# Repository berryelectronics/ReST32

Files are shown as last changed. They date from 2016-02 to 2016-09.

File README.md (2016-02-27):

# ReST32 - Modular, Open Source 3D Printer Controller
A modular 3D Printer Controller based on the STM32Duino project

This controller is using extra modules for the Heated Bed, Heaters, Extra Extruder Steppers aswell as extra PWM Output for fans and LED's. If you feel to upgrade your printer, just get the module for it. If you manage to damage the MosFET, just swap it out! This brings a low cost base platform, which you can upgrade freely.

- 72Mhz Cortex M3 (STM32F103V)
- 128kb Flash 
- 3 Axis Stepper + 3 Extruder Stepper (1 on the Mainboard)
- 6 Endstop Inputs
- 1 Heated Bed + 1 Thermistor
- 2 Heaters + 2 Thermistors
- High Efficiency 3.3V Buck Converter
- 12V Protected by a proper Car Fuse holder (Heatbed & Electronics)
- (currently) 4 0.6A 12V PWM Channels
- SPI, I2C and Parallel Pinout (Plans for a Full Color Touch GLCD)
- 4 Servo Pinout
- A bulk of Voltage Outputs at one place (4xGND, 4x3V3, 4x5V, 4x12V)

Planned Firmware support:
- Marlin

Modules available:
- Mainboard
- Heatbed Module with AOT240L MosFET and seperate fused 12V Input
- Heater Module with AOT240L MosFET
- Stepper Module to hold 2 more POLOLU Stepper Driver (for usage with dual extrusion or Diamond Hotend)
- Additional Module, with a ULN2803 Darlington Array and 4 0.6A Outputs, for Extruder Fans, LEDs, etc.

Images: 

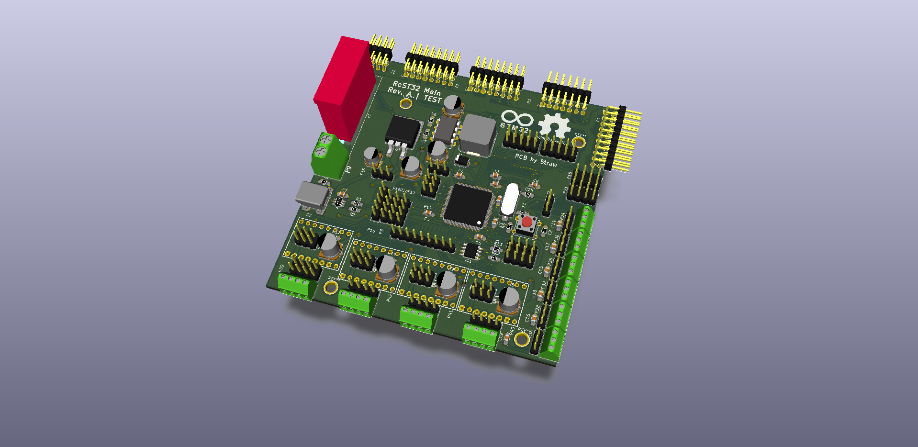
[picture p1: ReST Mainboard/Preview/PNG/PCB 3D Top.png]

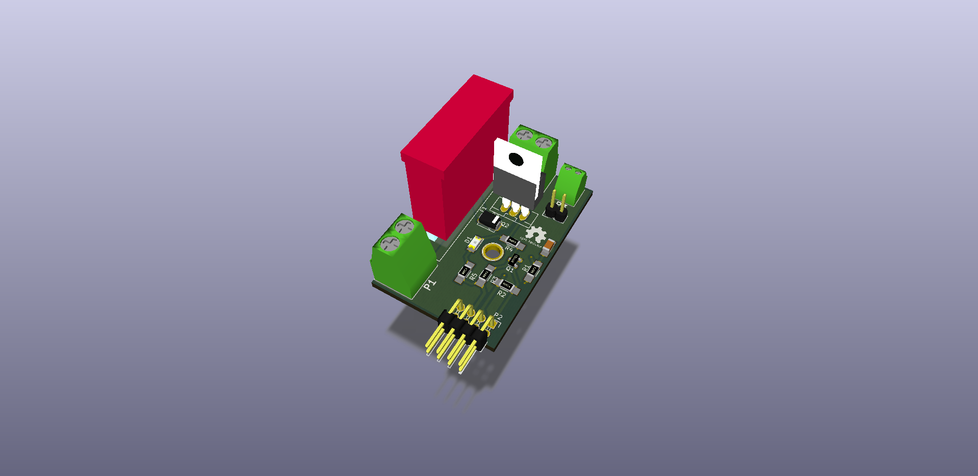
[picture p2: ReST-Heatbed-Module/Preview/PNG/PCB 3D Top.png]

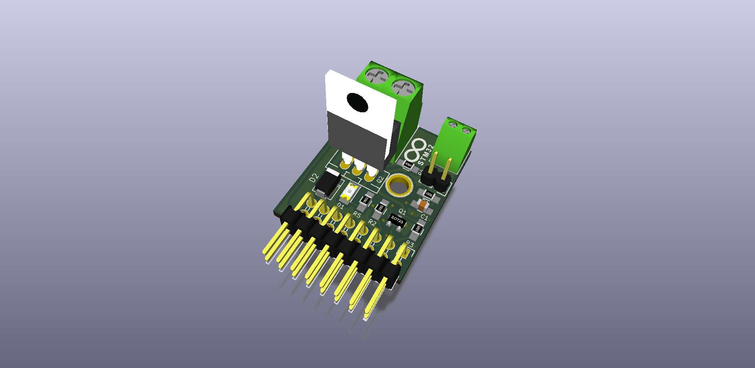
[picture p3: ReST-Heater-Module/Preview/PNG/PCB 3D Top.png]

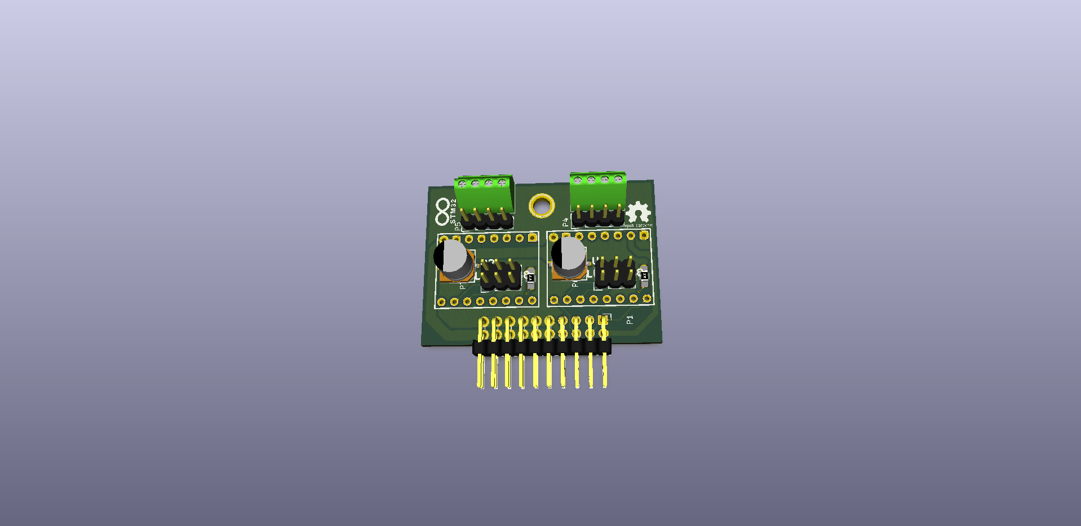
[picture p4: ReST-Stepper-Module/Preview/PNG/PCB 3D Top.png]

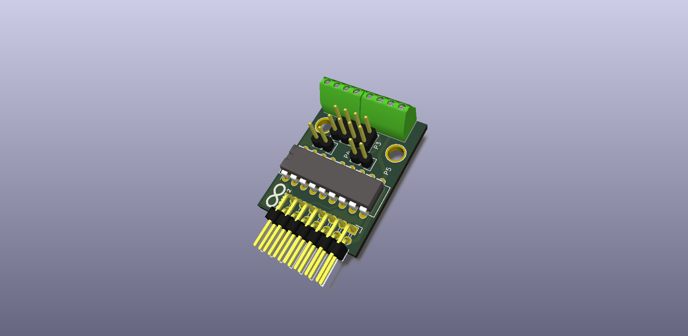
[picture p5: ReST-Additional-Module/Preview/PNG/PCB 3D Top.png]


Sources for Symbols, Footprints and 3D Symbols:

WIP

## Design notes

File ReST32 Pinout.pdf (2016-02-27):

PIN NAME | DEFAULT
1 PE2 | TRACECK/ FSMC_A23 | STEPPER | X-STEP
2 PE3 | TRACED0/FSMC_A19 | STEPPER | X-EN
3 PE4 | TRACED1/FSMC_A20 | ENDSTOP | Z-MAX
4 PE5 | TRACED2/FSMC_A21 | ENDSTOP | Z-MIN
5 PE6 | TRACED3/FSMC_A22 | ENDSTOP | Y-MAX
14 NRST | NRST | RESET | BUTTON SWD
15 PC0 | ADC123_IN10 | ENDSTOP | Y-MIN
16 PC1 | ADC123_IN11 | ENDSTOP | X-MAX
17 PC2 | ADC123_IN12 | ENDSTOP | X-MIN
18 PC3 | ADC123_IN13 | STEPPER | E1-DIR
23 PA0-WKUP | WKUP/USART2_CTS/ ADC123_IN0 /TIM2_CH1_ETR /TIM5_CH1/TIM8_ETR | STEPPER | E1-STEP
24 PA1 | USART2_RTS/ ADC123_IN1/ TIM5_CH2/TIM2_CH2 | STEPPER | E1-EN
25 PA2 | USART2_TX/TIM5_CH3 /ADC123_IN2/ TIM2_CH3 | STEPPER | E2-DIR
26 PA3 | USART2_RX/TIM5_CH4 /ADC123_IN3/TIM2_CH4 | STEPPER | E2-STEP
29 PA4 | SPI1_NSS/ USART2_CK /DAC_OUT1/ADC12_IN4 | STEPPER | E2-EN
30 PA5 | SPI1_SCK/ DAC_OUT2/ ADC12_IN5 | H/T | PWM-ADD0
31 PA6 | SPI1_MISO /TIM8_BKIN/ADC12_IN6 /TIM3_CH1 | H/T | PWM-HEAT1
32 PA7 | SPI1_MOSI/ TIM8_CH1N/ADC12_IN7 /TIM3_CH2 | H/T | PWM-HEAT0
33 PC4 | ADC12_IN14 | H/T | T2
34 PC5 | ADC12_IN15 | H/T | T1
35 PB0 | ADC12_IN8/TIM3_CH3 /TIM8_CH2N | H/T | T0
36 PB1 | ADC12_IN9/TIM3_CH4/ TIM8_CH3N | ADD | PWM-BED
38 PE7 | FSMC_D4 | LCD | LCD-D0
39 PE8 | FSMC_D5 | LCD | LCD-D1
40 PE9 | FSMC_D6 | LCD | LCD-D2
41 PE10 | FSMC_D7 | LCD | LCD-D3
42 PE11 | FSMC_D8 | LCD | LCD-D4
43 PE12 | FSMC_D9 | LCD | LCD-D5
44 PE13 | FSMC_D10 | LCD | LCD-D6
45 PE14 | FSMC_D11 | LCD | LCD-D7
46 PE15 | FSMC_D12 | LCD | LCD-CS
47 PB10 | I2C2_SCL/USART3_TX | LCD | LCD-CD

LCD Compatible with ADAFRUIT 2.8" 8080 Breakout

48 PB11 | I2C2_SDA/USART3_RX | LCD | LCD-WR
51 PB12 | SPI2_NSS/I2S2_WS/ I2C2_SMBA/ USART3_CK/ TIM1_BKIN | SPI | SPI-CS1
52 PB13 | SPI2_SCK/I2S2_CK /USART3_CTS/ TIM1_CH1N | SPI | SPI-SCK
53 PB14 | SPI2_MISO/TIM1_CH2N/ USART3_RTS | SPI | SPI-MISO
54 PB15 | SPI2_MOSI/I2S2_SD /TIM1_CH3N | SPI | SPI-MOSI
55 PD8 | FSMC_D13 | SPI | SPI-CS2
56 PD9 | FSMC_D14 | LCD | LCD-RD
57 PD10 | FSMC_D15 | SERVO | SERVO1
58 PD11 | FSMC_A16 | SERVO | SERVO2
59 PD12 | FSMC_A17 | SERVO | SERVO3
60 PD13 | FSMC_A18 | SERVO | SERVO4
61 PD14 | FSMC_D0 | EXTRA | EXTRA0
62 PD15 | FSMC_D1 | EXTRA | EXTRA1
63 PC6 | I2S2_MCK/ TIM8_CH1/SDIO_D6 | ADD | PWM-ADD3
64 PC7 | I2S3_MCK/ TIM8_CH2/SDIO_D7 | ADD | PWM-ADD2
65 PC8 | TIM8_CH3/SDIO_D0 | ADD | PWM-ADD1
66 PC9 | TIM8_CH4/SDIO_D1 | EXTRA | EXTRA2
67 PA8 | USART1_CK/ TIM1_CH1/MCO | EXTRA | EXTRA3
68 PA9 | USART1_TX/ TIM1_CH2 | UART | UART1
69 PA10 | USART1_RX/ TIM1_CH3 | UART | UART1
70 PA11 | USART1_CTS/USBDM CAN_RX/TIM1_CH4 | USB | USB-DM
71 PA12 | USART1_RTS/USBDP/ CAN_TX/TIM1_ETR | USB | USB-DP
72 PA13 | JTMS-SWDIO | SWD | SWDIO
76 PA14 | JTCK-SWCLK | SWD | SWDCLK
78 PC10 | UART4_TX/SDIO_D2 | EXTRA | EXTRA4
79 PC11 | UART4_RX/SDIO_D3 | EXTRA | EXTRA5
80 PC12 | UART5_TX/SDIO_CK | BL | UART5-TX
83 PD2 | TIM3_ETR/UART5_RX /SDIO_CMD | BL | UART5-RX
84 PD3 | FSMC_CLK | STEPPER | Z-DIR
85 PD4 | FSMC_NOE | STEPPER | Z-STEP
86 PD5 | FSMC_NWE | STEPPER | Z-EN
87 PD6 | FSMC_NWAIT | STEPPER | E0-DIR
88 PD7 | FSMC_NE1/FSMC_NCE2 | STEPPER | E0-STEP

91 PB5 | I2C1_SMBA/ SPI3_MOSI/ I2S3_SD | STEPPER | E0-EN
92 PB6 | I2C1_SCL/ TIM4_CH1 | I2C | I2C-SCL
93 PB7 | I2C1_SDA / FSMC_NADV / TIM4_CH2 | I2C | I2C_SDA
95 PB8 | TIM4_CH3/SDIO_D4 | STEPPER | Y-DIR
96 PB9 | TIM4_CH4/SDIO_D5 | STEPPER | Y-STEP
97 PE0 | TIM4_ETR / FSMC_NBL0 | STEPPER | Y-EN
98 PE1 | FSMC_NBL1 | STEPPER | X-DIR

LCD Compatible with ADAFRUIT 2.8" 8080 Breakout

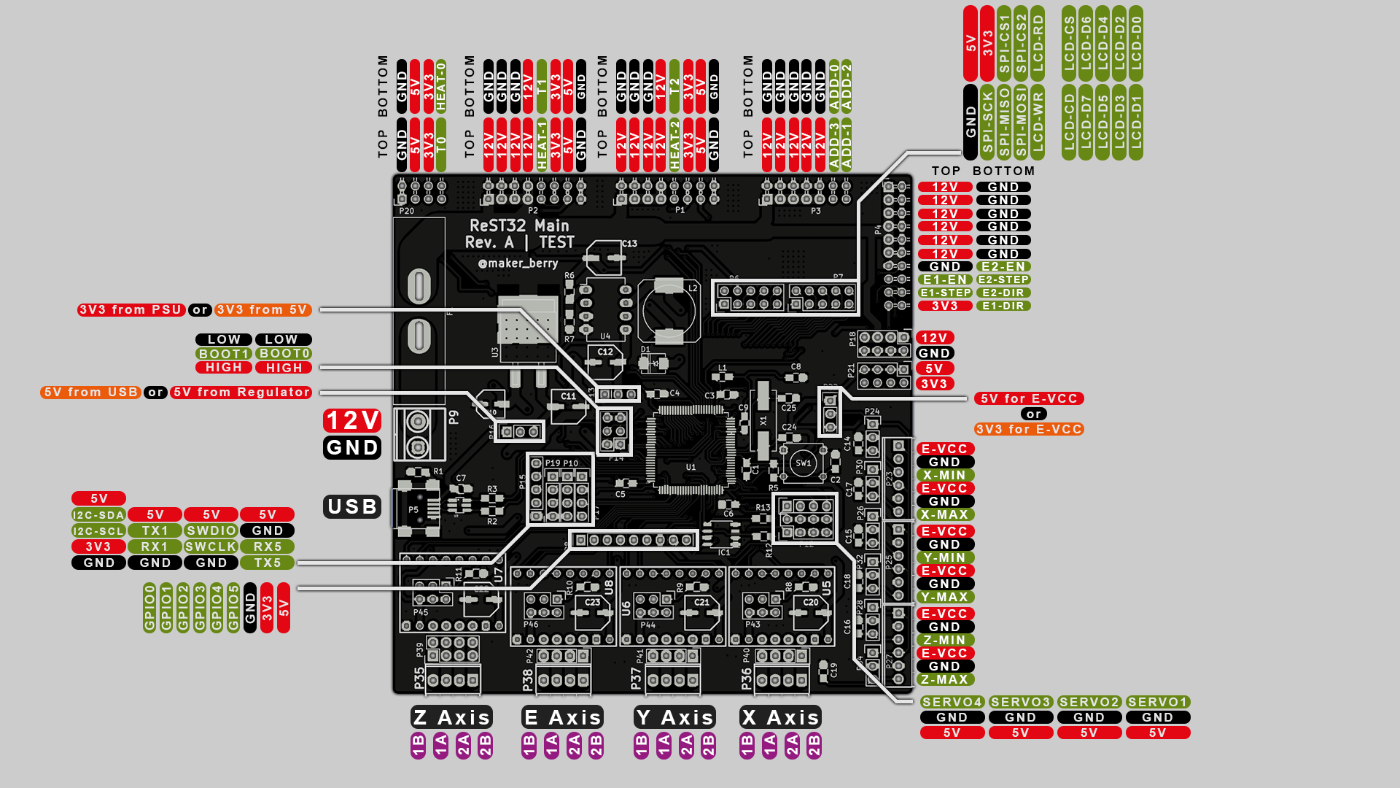
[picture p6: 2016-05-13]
ReST32 Pinout.png

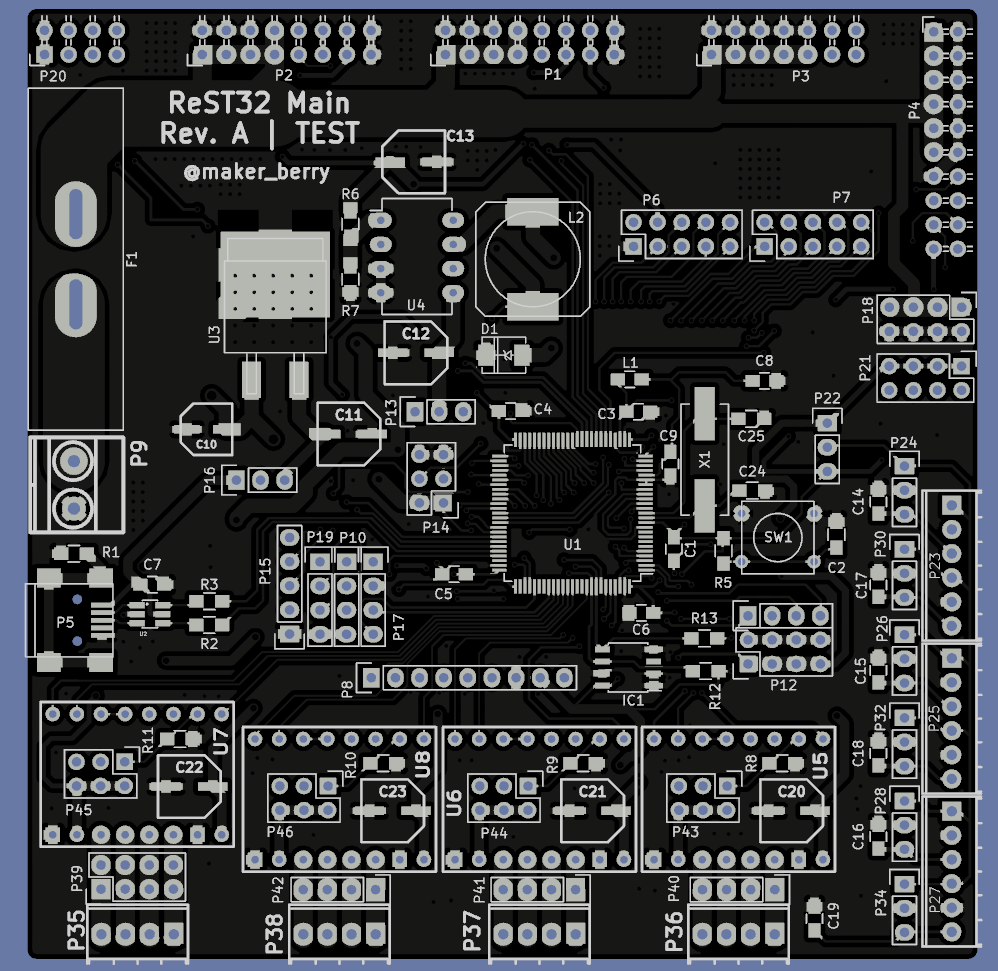
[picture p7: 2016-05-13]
Mainboard Image.png

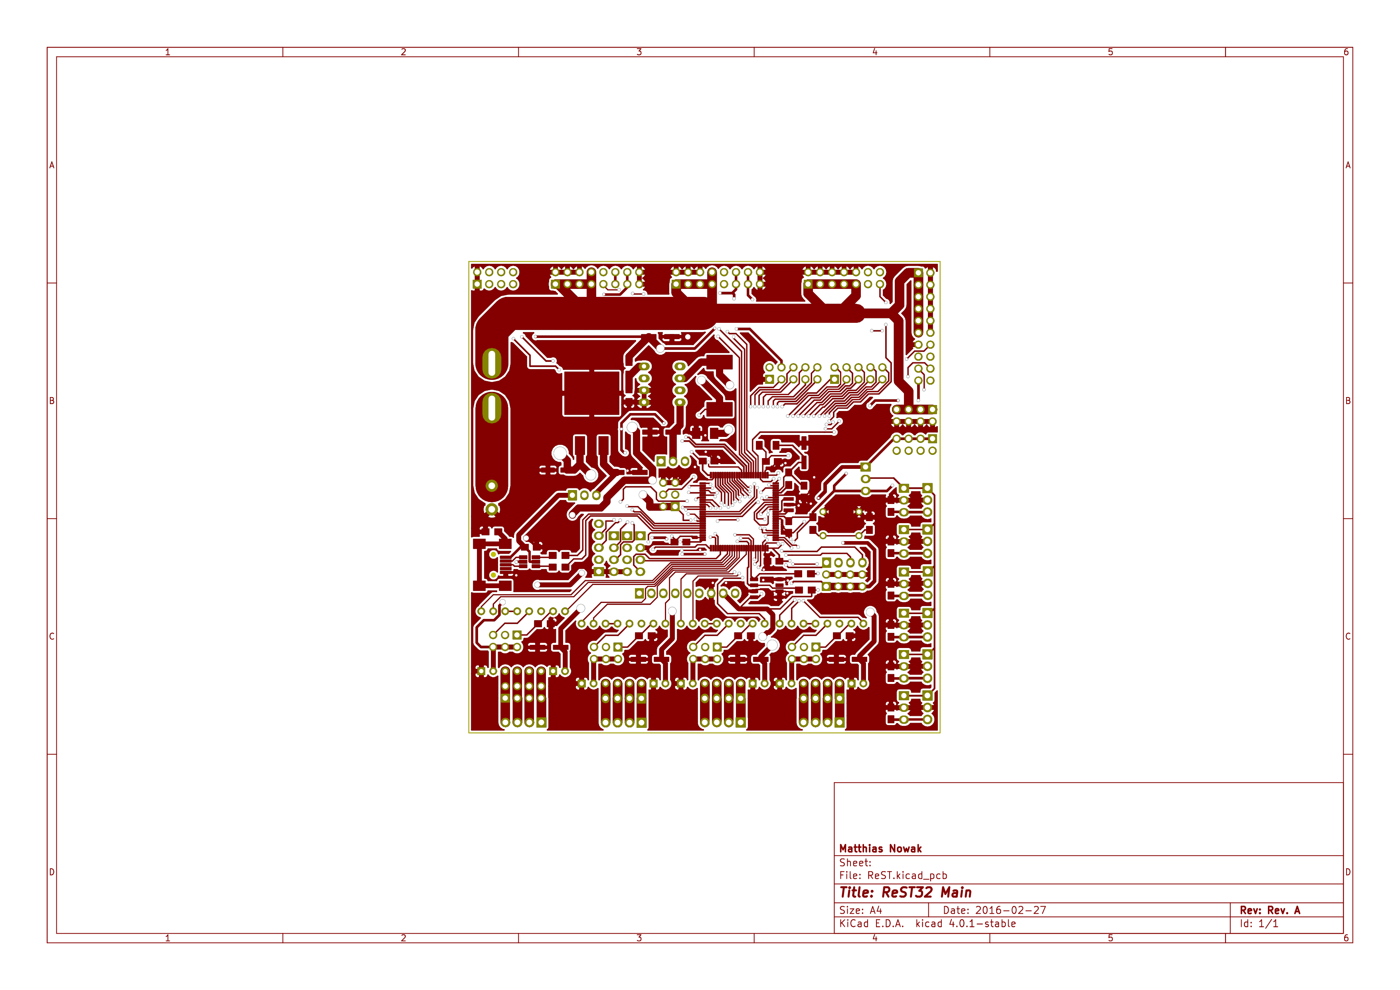
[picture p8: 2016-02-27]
ReST Mainboard - Hierarchical/Preview/PNG/PCB Front.png

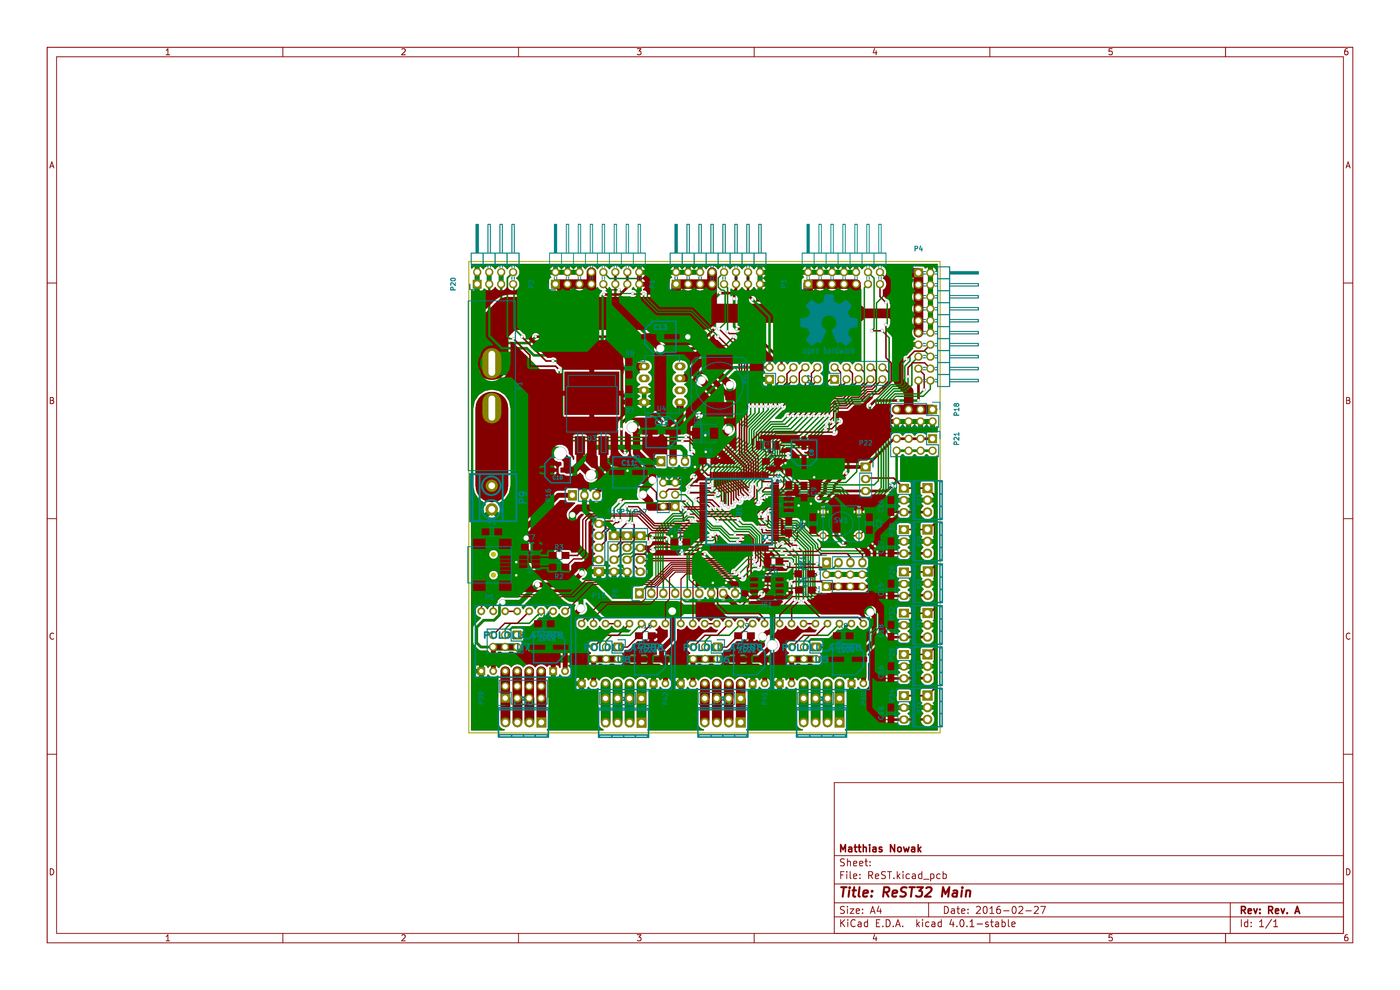
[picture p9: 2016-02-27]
ReST Mainboard - Hierarchical/Preview/PNG/PCB Full.png

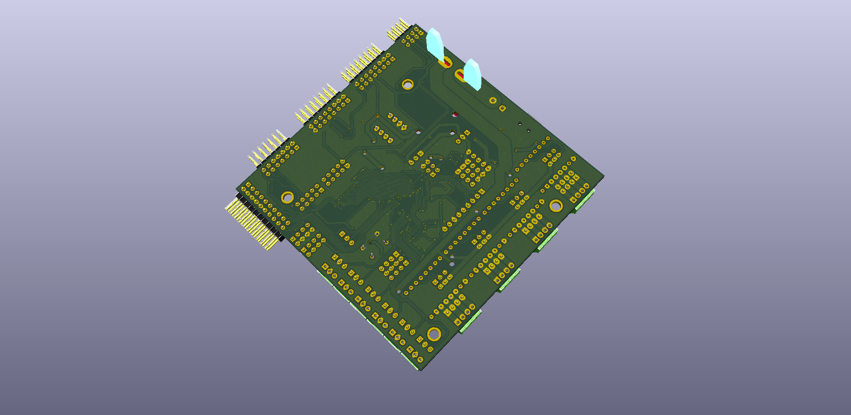
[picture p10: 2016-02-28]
ReST Mainboard - Hierarchical/Preview/PNG/PCB 3D Bottom.png

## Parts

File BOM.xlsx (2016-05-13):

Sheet: Stepper Module
Number | Reference | Description | Quantity | Price | Ali Link | Quantity | Price
1 | R1, R2 | Resistor 100K 0805 | 2 | 0.01 | http://goo.gl/Uvxbzr | 200 | 0.55
2 | C1, C2 | Capacitor 100uF 35V Panasonic D8 | 2 | 0.26 | http://goo.gl/ltnznB | 20 | 2.42
3 | U1, U2 | Female Pinheader Straight 2.54mm 1x8 | 4 | 0.16 | http://goo.gl/x2I61O | 100 | 3.34
4 | P4, P5 | Male Pinheader Straight 2.54mm 1x4 | 2 | 0.02 | http://goo.gl/sHfYwQ | 10 * 40 | 0.61
5 | P6, P7 | Male Pinheader Straight 2.54mm 2x3 | 2 | 0.03 | http://goo.gl/4wHt0U | 5 * 40 | 0.89
6 | P1 | Female Pinheader Angled 2.54mm 2x10 | 1 | 0.2 | http://goo.gl/Tiwzux | 5 * 40 | 3.43
7 | P2, P3 | Screw Terminal 2.54mm 4P | 2 | 0.68 | http://goo.gl/5jTE6Z | 10 | 3.33
- | PCB | Stepper Module PCB | 1 | 0.6
 |  |  | Total Price | 1.96

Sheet: SD Module
Number | Reference | Description | Quantity | Price | Ali Link | Quantity | Price
1 | CON1 | uSD Card Socket | 1 | 0.26 | http://goo.gl/VlQFaa | 10 | 2.59
2 | D1 | LED White 1206 3.0-3.6V | 1 | 0.02 | http://goo.gl/arnBD1 | 100 | 1.24
3 | R1 | Resistor 10K 0805 | 1 | 0.01 | http://goo.gl/0wMJSf | 200 | 0.55
4 | R2 | Resistor 150R 0805 | 1 | 0.01 | http://goo.gl/dDApy1 | 200 | 0.55
5 | C1 | Capacitor 100nF 0805 | 1 | 0.01 | http://goo.gl/qXetTo | 100 | 0.7
6 | P1 | Female Pinheader Straight 2.54mm 2x5 | 1 | 0.07 | http://goo.gl/c0pA5g | 10 | 0.59
- | PCB | SD Module PCB | 1 | 0.6
 |  |  | Total Price | 0.98

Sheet: Heater Module
Number | Reference | Description | Quantity | Price | Ali Link | Quantity | Price
1 | Q1 | BSH105 Mosfet SOT23 | 1 | 0.15 | http://goo.gl/TvNGQm | 20 | 2.8
2 | Q2 | AOT240L Mosfet TO-220 | 1 | 0.53 | http://goo.gl/u8gwWL | 20 | 10.56
3 | D1 | LED White 1206 3.0-3.6V | 1 | 0.02 | http://goo.gl/arnBD1 | 100 | 1.24
4 | D2 | 1N4007 SMD DO-214AC | 1 | 0.02 | http://goo.gl/DEAsnl | 100 | 1.21
5 | R1 | Resistor 4K7 0805 | 1 | 0.01 | http://goo.gl/WeyGSC | 200 | 0.55
6 | R2, R3 | Resistor 100K 0805 | 2 | 0.01 | http://goo.gl/T7ThLM | 200 | 0.55
7 | R4 | Resistor 22R 0805 | 1 | 0.01 | http://goo.gl/3FQRHP | 200 | 0.55
8 | R5 | Resistor 150R 0805 | 1 | 0.01 | http://goo.gl/dDApy1 | 200 | 0.55
9 | C1 | Capacitor 10uF 0805 | 1 | 0.02 | http://goo.gl/QtQfQl | 50 | 0.92
10 | P4 | Male Pinheader Straight 2.54mm 1x2 | 1 | 0.1 | http://goo.gl/sHfYwQ | 10 * 40 | 0.61
11 | P1 | Female Pinheader Angled 2.54mm 2x8 | 1 | 0.2 | http://goo.gl/Tiwzux | 5 * 40 | 3.43
12 | P3 | Screw Terminal 2.54mm 2P | 1 | 0.2 | http://goo.gl/k6Y1PR | 20 | 3.7
- | PCB | Heater PCB | 1 | 0.6
 |  |  | Total Price | 1.88

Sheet: Heatbed Module
Number | Reference | Description | Quantity | Price | Ali Link | Quantity | Price
1 | Q1 | BSH105 Mosfet SOT23 | 1 | 0.15 | http://goo.gl/TvNGQm | 20 | 2.8
2 | Q2 | AOT240L Mosfet TO-220 | 1 | 0.53 | http://goo.gl/u8gwWL | 20 | 10.56
3 | D1 | LED White 1206 3.0-3.6V | 1 | 0.02 | http://goo.gl/arnBD1 | 100 | 1.24
4 | D2 | 1N4007 SMD DO-214AC | 1 | 0.02 | http://goo.gl/DEAsnl | 100 | 1.21
5 | R1 | Resistor 4K7 0805 | 1 | 0.01 | http://goo.gl/WeyGSC | 200 | 0.55
6 | R2, R3 | Resistor 100K 0805 | 2 | 0.01 | http://goo.gl/T7ThLM | 200 | 0.55
7 | R4 | Resistor 22R 0805 | 1 | 0.01 | http://goo.gl/3FQRHP | 200 | 0.55
8 | R5 | Resistor 150R 0805 | 1 | 0.01 | http://goo.gl/dDApy1 | 200 | 0.55
9 | C1 | Capacitor 10uF 0805 | 1 | 0.02 | http://goo.gl/QtQfQl | 50 | 0.92
10 | P4 | Male Pinheader Straight 2.54mm 1x2 | 1 | 0.1 | http://goo.gl/sHfYwQ | 10 * 40 | 0.61
11 | P1 | Female Pinheader Angled 2.54mm 2x4 | 1 | 0.1 | http://goo.gl/Tiwzux | 5 * 40 | 3.43
12 | P3 | Screw Terminal 2.54mm 2P | 1 | 0.2 | http://goo.gl/k6Y1PR | 20 | 3.7
13 | P5 | Screw Terminal 5.08mm 2P | 1 | 0.32 | http://goo.gl/4nj4FG | 20 | 3.04
14 | F1 | ATC Fuse holder | 1 | 0.24 | http://goo.gl/RVs7Jv | 20 | 4.64
- | PCB | Heatbed PCB | 1 | 0.6
 |  |  | Total Price | 2.34

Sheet: Additional IRLML2502 Module
Number | Reference | Description | Quantity | Price | Ali Link | Quantity | Price
1 | Q1-Q4 | IRLML2502 | 4 | 0.2 | http://goo.gl/9asYlu | 100 | 4.76
2 | R1, R2, R5, R6 | Resistor 27R 0805 | 4 | 0.02 | http://goo.gl/fIMej5 | 200 | 0.55
3 | R3, R4, R7, R8 | Resistor 100K 0805 | 4 | 0.02 | http://goo.gl/57JWqM | 200 | 0.55
4 | P2 | Male Pinheader Straight 2.54mm 1x8 | 1 | 0.02 | http://goo.gl/sHfYwQ | 10 * 40 | 0.61
5 | P1 | Female Pinheader Angled 2.54mm 2x7 | 1 | 0.2 | http://goo.gl/Tiwzux | 5 * 40 | 3.43
6 | P3, P4 | Screw Terminal 2.54mm 4P | 2 | 0.63 | http://goo.gl/5jTE6Z | 10 | 3.33
- | PCB | Additional IRLML2502 PCB | 1 | 0.6
 |  |  | Total Price | 1.69

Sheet: Mainboard
Number | Reference | Description | Quantity | Price | Ali Link | Quantity | Price
1 | U1 | STM32F103V | 1 | 3.53 | http://goo.gl/SWVCW9 | 10 | 34.32
2 | U2 | USBLC6-2 | 1 | 0.15 | http://goo.gl/zFyJ8W | 20 | 2.79
3 | U3 | L7805ACD2T-TR | 1 | 0.32 | http://goo.gl/RYbWXG | 30 | 9.37
4 | U4 | LM2574N-ADJ | 1 | 0.86 | http://goo.gl/atzKwN | 10 | 8.54
5 | U4-2 | 8 PIN DIP Socket | 1 | 0.03 | http://goo.gl/aslodI | 60 | 1.67
6 | IC1 | AT24C128/AT24C256 SOP-8 | 1 | 0.23 | http://goo.gl/rgJsQZ | 20 | 2.21
7 | P5 | Mini USB | 1 | 0.23 | http://goo.gl/R6B4Uv | 5 | 1.1
8 | X1 | 8Mhz HC49-SD SMD | 1 | 0.09 | http://goo.gl/8yFClU | 20 | 1.61
9 | L1 | Ferrite bead 0805 | 1 | 0.02 | http://goo.gl/pLQdhZ | 100 | 1.85
10 | L2 | Inductor 330uH 1A CD127 | 1 | 0.22 | http://goo.gl/zI73sO | 20 | 3.92
11 | D1 | 1N5819 SMD DO-214AC | 1 | 0.01 | http://goo.gl/TtCLTt | 100 | 0.91
12 | SW1 | Momentary push button 6*6*8mm PTH | 1 | 0.03 | http://goo.gl/xWl71v | 100 | 2.6
13 | SW1-2 | A56 Cap | 1 | 0.03 | http://goo.gl/cRQ3u8 | 100 | 2.69
14 | R1 | Resistor 1M 0805 | 1 | 0.04 | http://goo.gl/DLXDps | 200 | 0.55
15 | R5 | Resistor 10K 0805 | 1 | 0.01 | http://goo.gl/0wMJSf | 200 | 0.55
16 | R12, R13 | Resistor 4K7 0805 | 2 | 0.01 | http://goo.gl/J9CeW8 | 200 | 0.55
17 | R6 | Resistor 2K7 0805 | 1 | 0.01 | http://goo.gl/o9DHvs | 200 | 0.55
18 | R7 | Resistor 1K6 0805 | 1 | 0.01 | http://goo.gl/1cEfEj | 200 | 0.55
19 | R8-R11 | Resistor 100K 0805 | 4 | 0.02 | http://goo.gl/57JWqM | 200 | 0.55
20 | R2, R3 | Resistor 22R | 2 | 0.01 | http://goo.gl/3FQRHP | 200 | 0.55
21 | C1-C7, C9 | Capacitor 100nF 0805 | 8 | 0.06 | http://goo.gl/qXetTo | 100 | 0.7
22 | C14-C19 | Capacitor 10nF 0805 | 6 | 0.05 | http://goo.gl/jdiYYI | 100 | 0.7
23 | C24, C25 | Capacitor 30pF 0805 | 2 | 0.02 | http://goo.gl/kIr8cb | 100 | 0.72
24 | C8 | Capacitor 10uF 0805 | 1 | 0.02 | http://goo.gl/QtQfQl | 50 | 0.92
25 | C10 | Capacitor 10uF Panasonic C 35V | 1 | 0.1 | http://goo.gl/zm18n2 | 20 | 1.81
26 | C11, C12 | Capacitor 22uF Panasonic D 35V | 2 | 0.2 | http://goo.gl/S5xocq | 20 | 1.72
27 | C13 | Capacitor 220uF Panasonic D 10V | 1 | 0.1 | http://goo.gl/kbIxif | 20 | 1.81
28 | C20-C23 | Capacitor 100uF Panasonic D8 35V | 4 | 0.52 | http://goo.gl/ltnznB | 20 | 2.42
29 | U5-U8 | Female Pinheader Straight 2.54mm 1x8 | 8 | 0.32 | http://goo.gl/x2I61O | 100 | 3.34
30 | P22-P34 EVEN, P13, P16 | Male Pinheader Straight 2.54mm 1x3 | 8 | 0.04 | http://goo.gl/sHfYwQ | 10 * 40 | 0.61
31 | P40-P42, P10, P17, P19, P11 | Male Pinheader Straight 2.54mm 1x4 | 7 | 0.05 | http://goo.gl/sHfYwQ | 10 * 40 | 0.61
32 | P15 | Male Pinheader Straight 2.54mm 1x5 | 1 | 0.01 | http://goo.gl/sHfYwQ | 10 * 40 | 0.61
33 | P8 | Male Pinheader Straight 2.54mm 1x9 | 1 | 0.02 | http://goo.gl/sHfYwQ | 10 * 40 | 0.61
34 | P43-P46, P14 | Male Pinheader Straight 2.54mm 2x3 | 5 | 0.07 | http://goo.gl/4wHt0U | 5 * 40 | 0.89
35 | P18, P21, P39, P12 | Male Pinheader Straight 2.54mm 2x4 | 4 | 0.08 | http://goo.gl/4wHt0U | 5 * 40 | 0.89
36 | P6, P7 | Male Pinheader Straight 2.54mm 2x5 | 2 | 0.05 | http://goo.gl/4wHt0U | 5 * 40 | 0.89
37 | P1, P2 | Male Pinheader Angled 2.54mm 2x8 | 2 | 0.12 | http://goo.gl/b7c1am | 10 * 40 | 2.78
38 | P3 | Male Pinheader Angled 2.54mm 2x7 | 1 | 0.05 | http://goo.gl/b7c1am | 10 * 40 | 2.78
39 | P4 | Male Pinheader Angled 2.54mm 2x10 | 1 | 0.07 | http://goo.gl/b7c1am | 10 * 40 | 2.78
40 | P20 | Male Pinheader Angled 2.54mm 2x4 | 1 | 0.03 | http://goo.gl/b7c1am | 10 * 40 | 2.78
41 | P23, P25, P27 | Screw Terminal 2.54mm 6P | 3 | 1.41 | http://goo.gl/ptDWCX | 10 | 4.63
42 | P35-P38 | Screw Terminal 2.54mm 4P | 4 | 1.26 | http://goo.gl/5jTE6Z | 10 | 3.33
43 | P9 | Screw Terminal 5.08mm 2P | 1 | 0.16 | http://goo.gl/4nj4FG | 20 | 3.04
44 | F1 | ATC Fuse holder | 1 | 0.24 | http://goo.gl/RVs7Jv | 20 | 4.64
- | PCB | Mainboard PCB | 1 | 4.5
 |  |  | Total Cost | 15.41

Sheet: Order List
Number | Description | Quantity | Price | Ali Link | Quantity | Price
1 | STM32F103V | 1 | 3.53 | http://goo.gl/SWVCW9 | 10 | 34.32
2 | USBLC6-2 | 1 | 0.15 | http://goo.gl/zFyJ8W | 20 | 2.79
3 | L7805ACD2T-TR | 1 | 0.32 | http://goo.gl/RYbWXG | 30 | 9.37
4 | LM2574N-ADJ | 1 | 0.86 | http://goo.gl/atzKwN | 10 | 8.54
5 | 8 PIN DIP Socket | 1 | 0.03 | http://goo.gl/aslodI | 60 | 1.67
6 | AT24C128/AT24C256 SOP-8 | 1 | 0.23 | http://goo.gl/rgJsQZ | 20 | 2.21
7 | Mini USB | 1 | 0.23 | http://goo.gl/R6B4Uv | 5 | 1.1
8 | 8Mhz HC49-SD SMD | 1 | 0.09 | http://goo.gl/8yFClU | 20 | 1.61
9 | Ferrite bead 0805 | 1 | 0.02 | http://goo.gl/pLQdhZ | 100 | 1.85
10 | Inductor 330uH 1A CD127 | 1 | 0.22 | http://goo.gl/zI73sO | 20 | 3.92
11 | 1N5819 SMD DO-214AC | 1 | 0.01 | http://goo.gl/TtCLTt | 100 | 0.91
12 | Momentary push button 6*6*8mm PTH | 1 | 0.03 | http://goo.gl/xWl71v | 100 | 2.6
14 | Resistor 1M 0805 | 1 | 0.04 | http://goo.gl/DLXDps | 200 | 0.55
15 | Resistor 10K 0805 | 2 | 0.02 | http://goo.gl/0wMJSf | 200 | 0.55
16 | Resistor 4K7 0805 | 5 | 0.03 | http://goo.gl/J9CeW8 | 200 | 0.55
17 | Resistor 2K7 0805 | 1 | 0.01 | http://goo.gl/o9DHvs | 200 | 0.55
18 | Resistor 1K6 0805 | 1 | 0.01 | http://goo.gl/1cEfEj | 200 | 0.55
19 | Resistor 100K 0805 | 13 | 0.04 | http://goo.gl/57JWqM | 200 | 0.55
20 | Resistor 22R | 5 | 0.01 | http://goo.gl/3FQRHP | 200 | 0.55
21 | Capacitor 100nF 0805 | 9 | 0.07 | http://goo.gl/qXetTo | 100 | 0.7
22 | Capacitor 10nF 0805 | 6 | 0.05 | http://goo.gl/jdiYYI | 100 | 0.7
23 | Capacitor 30pF 0805 | 2 | 0.02 | http://goo.gl/kIr8cb | 100 | 0.72
24 | Capacitor 10uF 0805 | 4 | 0.1 | http://goo.gl/QtQfQl | 50 | 0.92
25 | Capacitor 10uF Panasonic C 35V | 1 | 0.1 | http://goo.gl/zm18n2 | 20 | 1.81
26 | Capacitor 22uF Panasonic D 35V | 2 | 0.2 | http://goo.gl/S5xocq | 20 | 1.72
27 | Capacitor 220uF Panasonic D 10V | 1 | 0.1 | http://goo.gl/kbIxif | 20 | 1.81
28 | Capacitor 100uF Panasonic D8 35V | 6 | 0.75 | http://goo.gl/ltnznB | 20 | 2.42
29 | Female Pinheader Straight 2.54mm 1x8 | 12 | 0.42 | http://goo.gl/x2I61O | 100 | 3.34
30 | Male Pinheader Straight 2.54mm 1x90 | 1 | 0.15 | http://goo.gl/sHfYwQ | 10 * 40 | 0.61
34 | Male Pinheader Straight 2.54mm 2x100 | 1 | 0.45 | http://goo.gl/4wHt0U | 5 * 40 | 0.89
41 | Screw Terminal 2.54mm 6P | 3 | 1.41 | http://goo.gl/ptDWCX | 10 | 4.63
42 | Screw Terminal 2.54mm 4P | 8 | 2.72 | http://goo.gl/5jTE6Z | 10 | 3.33
43 | Screw Terminal 5.08mm 2P | 2 | 0.33 | http://goo.gl/4nj4FG | 20 | 3.04
44 | ATC Fuse holder | 2 | 0.5 | http://goo.gl/RVs7Jv | 20 | 4.64
1 | BSH105 Mosfet SOT23 | 3 | 0.45 | http://goo.gl/TvNGQm | 20 | 2.8
2 | AOT240L Mosfet TO-220 | 3 | 1.6 | http://goo.gl/Uk5B9L | 50 | 25.87
3 | LED White 1206 3.0-3.6V | 4 | 0.1 | http://goo.gl/arnBD1 | 100 | 1.24
4 | 1N4007 SMD DO-214AC | 3 | 0.06 | http://goo.gl/DEAsnl | 100 | 1.21
8 | Resistor 150R 0805 | 4 | 0.02 | http://goo.gl/dDApy1 | 200 | 0.55
11 | Female Pinheader Angled 2.54mm 2x42 | 1 | 0.75 | http://goo.gl/Tiwzux | 5 * 40 | 3.43 | 23.38
12 | Screw Terminal 2.54mm 2P | 3 | 0.6 | http://goo.gl/k6Y1PR | 20 | 3.7
1 | uSD Card Socket | 1 | 0.26 | http://goo.gl/VlQFaa | 10 | 2.59
6 | Female Pinheader Straight 2.54mm 2x5 | 1 | 0.07 | http://goo.gl/c0pA5g | 10 | 0.59
1 | IRLML2502 | 4 | 0.2 | http://goo.gl/9asYlu | 100 | 4.76
2 | Resistor 27R 0805 | 4 | 0.02 | http://goo.gl/fIMej5 | 200 | 0.55
- | PCB Main, HB, Heat*2, Extra, Stepper | 6 | 6

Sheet: Pers. Shopping List
Mainboard*10 | Heatbed*10 | Heater*15 | Additional*5 | Stepper*5 | SD*5
Number | Description | Quantity | Ali Link | Quantity | Price x Quan. | Order Quantity
1 | STM32F103V | 10 | http://goo.gl/SWVCW9 | 10 | 34.32
2 | USBLC6-2 | 10 | http://goo.gl/zFyJ8W | 20 | 2.79
3 | L7805ACD2T-TR | 10 | http://goo.gl/RYbWXG | 30 | 9.37
4 | LM2574N-ADJ | 10 | http://goo.gl/atzKwN | 10 | 8.54
5 | 8 PIN DIP Socket | 10 | http://goo.gl/aslodI | 60 | 1.67
6 | AT24C128/AT24C256 SOP-8 | 10 | http://goo.gl/rgJsQZ | 20 | 2.21
7 | Mini USB | 10 | http://goo.gl/R6B4Uv | 5 | 3.3 | x3
8 | 8Mhz HC49-SD SMD | 10 | http://goo.gl/8yFClU | 20 | 1.61
9 | Ferrite bead 0805 | 10 | http://goo.gl/pLQdhZ | 100 | 1.85
10 | Inductor 330uH 1A CD127 | 10 | http://goo.gl/zI73sO | 20 | 3.92
11 | 1N5819 SMD DO-214AC | 10 | http://goo.gl/TtCLTt | 100 | 0.91
12 | Momentary push button 6*6*8mm PTH | 10 | http://goo.gl/xWl71v | 100 | 2.6
13 | Resistor 1M 0805 | 10 | http://goo.gl/DLXDps | 200 | 0.55
14 | Resistor 10K 0805 | 15 | http://goo.gl/0wMJSf | 200 | 0.55
15 | Resistor 4K7 0805 | 45 | http://goo.gl/J9CeW8 | 200 | 0.55
16 | Resistor 2K7 0805 | 10 | http://goo.gl/o9DHvs | 200 | 0.55
17 | Resistor 1K6 0805 | 10 | http://goo.gl/1cEfEj | 200 | 0.55
18 | Resistor 100K 0805 | 80 | http://goo.gl/57JWqM | 200 | 0.55
19 | Resistor 22R | 25 | http://goo.gl/3FQRHP | 200 | 0.55
20 | Capacitor 100nF 0805 | 85 | http://goo.gl/qXetTo | 100 | 1.4 | x2
21 | Capacitor 10nF 0805 | 60 | http://goo.gl/jdiYYI | 100 | 0.7
22 | Capacitor 30pF 0805 | 20 | http://goo.gl/kIr8cb | 100 | 0.72
23 | Capacitor 10uF 0805 | 35 | http://goo.gl/QtQfQl | 50 | 1.84 | x2
24 | Capacitor 10uF Panasonic C 35V | 10 | http://goo.gl/zm18n2 | 20 | 1.81
25 | Capacitor 22uF Panasonic D 35V | 20 | http://goo.gl/S5xocq | 20 | 3.44 | x2
26 | Capacitor 220uF Panasonic D 10V | 10 | http://goo.gl/kbIxif | 20 | 1.81
27 | Capacitor 100uF Panasonic D8 35V | 50 | http://goo.gl/ltnznB | 20 | 7.26 | x3
28 | Female Pinheader Straight 2.54mm 1x8 | 100 | http://goo.gl/x2I61O | 100 | 6.68 | x2
29 | Male Pinheader Straight 2.54mm 1x90 | 10 | http://goo.gl/sHfYwQ | 10 * 40 | 1.83 | x3
30 | Male Pinheader Straight 2.54mm 2x100 | 8 | http://goo.gl/4wHt0U | 5 * 40 | 3.56 | x4 | oder x5
31 | Screw Terminal 2.54mm 6P | 30 | http://goo.gl/ptDWCX | 10 | 13.89 | x3
32 | Screw Terminal 2.54mm 4P | 60 | http://goo.gl/5jTE6Z | 10 | 19.98 | x6
33 | Screw Terminal 5.08mm 2P | 20 | http://goo.gl/4nj4FG | 20 | 3.04
34 | ATC Fuse holder | 20 | http://goo.gl/RVs7Jv | 20 | 4.64
35 | BSH105 Mosfet SOT23 | 25 | http://goo.gl/TvNGQm | 20 | 5.6 | x2
36 | AOT240L Mosfet TO-220 | 25 | http://goo.gl/Uk5B9L | 50 | 25.87
37 | LED White 1206 3.0-3.6V | 30 | http://goo.gl/arnBD1 | 100 | 1.24
38 | 1N4007 SMD DO-214AC | 25 | http://goo.gl/DEAsnl | 100 | 1.21
39 | Resistor 150R 0805 | 30 | http://goo.gl/dDApy1 | 200 | 0.55
40 | Female Pinheader Angled 2.54mm 2x40 | 4 | http://goo.gl/Tiwzux | 5 * 40 | 3.43
41 | Screw Terminal 2.54mm 2P | 25 | http://goo.gl/k6Y1PR | 20 | 7.4 | x2
42 | uSD Card Socket | 5 | http://goo.gl/VlQFaa | 10 | 2.59
43 | Female Pinheader Straight 2.54mm 2x5 | 5 | http://goo.gl/c0pA5g | 10 | 0.59
44 | IRLML2502 | 20 | http://goo.gl/9asYlu | 100 | 4.76
45 | Resistor 27R 0805 | 20 | http://goo.gl/fIMej5 | 200 | 0.55
46 | Platinen | 10 |  | 1*10 | 65
47
48 |  |  | BESTELLUNG TOTAL |  | 268.33
49
50
51
52
53
54
55
56
57
58
59
60
61
62
63
64
65
66
67
68
69
70
71
72
73
74
75
76
77
78
79
80
81
82
83
84
85
86
87
88
89
90
91
92
93
94
95
96
97
98
99
100
101
102
103
104
105
106
107
108
109
110
111
112
113
114
115
116
117
118
119

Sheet: New Thing V2
Fuse holder | http://de.farnell.com/keystone/3544/fuse-holder-0-8-x-2-8mm-pcb-mount/dp/2301268

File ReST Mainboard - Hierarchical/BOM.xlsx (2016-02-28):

version | source | date | tool | number | name | tstamps | title | company | rev | date2 | source3 | number4 | value | ref | value5 | footprint | lib | part | names | tstamps6 | tstamp | lib7 | part8 | alias | description | fp | field | name9 | num | name10 | type | docs | logical | uri | code | name11 | ref12 | pin
D |  |  |  |  |  |  |  |  |  |  |  |  |  | X1 | 8MHZ RESONATOR | ReST-Library:SMD-3P | device | CRYSTAL_SMD | / | / | 56A465D2
D |  |  |  |  |  |  |  |  |  |  |  |  |  | P20 | CONN_02X04 | Pin_Headers:Pin_Header_Angled_2x04 | conn | CONN_02X04 | / | / | 56ACDC5B
D |  |  |  |  |  |  |  |  |  |  |  |  |  | U5 | POLOLU_A4988 | ReST-Library:SWDIP8_.6W | pololu_a4988 | POLOLU_A4988 | / | / | 56B13824
D |  |  |  |  |  |  |  |  |  |  |  |  |  | P43 | CONN_02X03 | Pin_Headers:Pin_Header_Straight_2x03 | conn | CONN_02X03 | / | / | 56B13885
D |  |  |  |  |  |  |  |  |  |  |  |  |  | P36 | SCREW_01X04 | 2:mpt_0,5%2f4-2,54 | conn | CONN_01X04 | / | / | 56B139B1
D |  |  |  |  |  |  |  |  |  |  |  |  |  | P24 | CONN_01X03 | Pin_Headers:Pin_Header_Straight_1x03 | conn | CONN_01X03 | / | / | 56B13BB0
D |  |  |  |  |  |  |  |  |  |  |  |  |  | P23 | SCREW_01X03 | 2:mpt_0,5%2f3-2,54 | conn | CONN_01X03 | / | / | 56B13C30
D |  |  |  |  |  |  |  |  |  |  |  |  |  | C14 | 10nF | Capacitors_SMD:C_0805_HandSoldering | device | C_Small | / | / | 56B13CD9
D |  |  |  |  |  |  |  |  |  |  |  |  |  | C20 | 100uF | ok-polcaps-panasonic:CP-PANASONIC-SMT_D8 | device | CP1_Small | / | / | 56B13DB2
D |  |  |  |  |  |  |  |  |  |  |  |  |  | R8 | 100K | Resistors_SMD:R_0805_HandSoldering | device | R_Small | / | / | 56B13E7B
D |  |  |  |  |  |  |  |  |  |  |  |  |  | U6 | POLOLU_A4988 | ReST-Library:SWDIP8_.6W | pololu_a4988 | POLOLU_A4988 | / | / | 56B56E17
D |  |  |  |  |  |  |  |  |  |  |  |  |  | P44 | CONN_02X03 | Pin_Headers:Pin_Header_Straight_2x03 | conn | CONN_02X03 | / | / | 56B56E1D
D |  |  |  |  |  |  |  |  |  |  |  |  |  | P37 | SCREW_01X04 | 2:mpt_0,5%2f4-2,54 | conn | CONN_01X04 | / | / | 56B56E29
D |  |  |  |  |  |  |  |  |  |  |  |  |  | C21 | 100uF | ok-polcaps-panasonic:CP-PANASONIC-SMT_D8 | device | CP1_Small | / | / | 56B56E2F
D |  |  |  |  |  |  |  |  |  |  |  |  |  | R9 | 100K | Resistors_SMD:R_0805_HandSoldering | device | R_Small | / | / | 56B56E35
D |  |  |  |  |  |  |  |  |  |  |  |  |  | U7 | POLOLU_A4988 | ReST-Library:SWDIP8_.6W | pololu_a4988 | POLOLU_A4988 | / | / | 56B585EB
D |  |  |  |  |  |  |  |  |  |  |  |  |  | P45 | CONN_02X03 | Pin_Headers:Pin_Header_Straight_2x03 | conn | CONN_02X03 | / | / | 56B585F1
D |  |  |  |  |  |  |  |  |  |  |  |  |  | P39 | CONN_02X04 | Pin_Headers:Pin_Header_Straight_2x04 | conn | CONN_02X04 | / | / | 56B585F7
D |  |  |  |  |  |  |  |  |  |  |  |  |  | P35 | SCREW_01X04 | 2:mpt_0,5%2f4-2,54 | conn | CONN_01X04 | / | / | 56B585FD
D |  |  |  |  |  |  |  |  |  |  |  |  |  | C22 | 100uF | ok-polcaps-panasonic:CP-PANASONIC-SMT_D8 | device | CP1_Small | / | / | 56B58603
D |  |  |  |  |  |  |  |  |  |  |  |  |  | R11 | 100K | Resistors_SMD:R_0805_HandSoldering | device | R_Small | / | / | 56B58609
D |  |  |  |  |  |  |  |  |  |  |  |  |  | U8 | POLOLU_A4988 | ReST-Library:SWDIP8_.6W | pololu_a4988 | POLOLU_A4988 | / | / | 56B58669
D |  |  |  |  |  |  |  |  |  |  |  |  |  | P46 | CONN_02X03 | Pin_Headers:Pin_Header_Straight_2x03 | conn | CONN_02X03 | / | / | 56B5866F
D |  |  |  |  |  |  |  |  |  |  |  |  |  | P38 | SCREW_01X04 | 2:mpt_0,5%2f4-2,54 | conn | CONN_01X04 | / | / | 56B5867B
D |  |  |  |  |  |  |  |  |  |  |  |  |  | C23 | 100uF | ok-polcaps-panasonic:CP-PANASONIC-SMT_D8 | device | CP1_Small | / | / | 56B58681
D |  |  |  |  |  |  |  |  |  |  |  |  |  | R10 | 100K | Resistors_SMD:R_0805_HandSoldering | device | R_Small | / | / | 56B58687
D |  |  |  |  |  |  |  |  |  |  |  |  |  | P30 | CONN_01X03 | Pin_Headers:Pin_Header_Straight_1x03 | conn | CONN_01X03 | / | / | 56B5FE78
D |  |  |  |  |  |  |  |  |  |  |  |  |  | P29 | SCREW_01X03 | 2:mpt_0,5%2f3-2,54 | conn | CONN_01X03 | / | / | 56B5FE7E
D |  |  |  |  |  |  |  |  |  |  |  |  |  | C17 | 10nF | Capacitors_SMD:C_0805_HandSoldering | device | C_Small | / | / | 56B5FE84
D |  |  |  |  |  |  |  |  |  |  |  |  |  | P26 | CONN_01X03 | Pin_Headers:Pin_Header_Straight_1x03 | conn | CONN_01X03 | / | / | 56B60284
D |  |  |  |  |  |  |  |  |  |  |  |  |  | P25 | SCREW_01X03 | 2:mpt_0,5%2f3-2,54 | conn | CONN_01X03 | / | / | 56B6028A
D |  |  |  |  |  |  |  |  |  |  |  |  |  | C15 | 10nF | Capacitors_SMD:C_0805_HandSoldering | device | C_Small | / | / | 56B60290
D |  |  |  |  |  |  |  |  |  |  |  |  |  | P32 | CONN_01X03 | Pin_Headers:Pin_Header_Straight_1x03 | conn | CONN_01X03 | / | / | 56B602AB
D |  |  |  |  |  |  |  |  |  |  |  |  |  | P31 | SCREW_01X03 | 2:mpt_0,5%2f3-2,54 | conn | CONN_01X03 | / | / | 56B602B1
D |  |  |  |  |  |  |  |  |  |  |  |  |  | C18 | 10nF | Capacitors_SMD:C_0805_HandSoldering | device | C_Small | / | / | 56B602B7
D |  |  |  |  |  |  |  |  |  |  |  |  |  | P28 | CONN_01X03 | Pin_Headers:Pin_Header_Straight_1x03 | conn | CONN_01X03 | / | / | 56B60BD8
D |  |  |  |  |  |  |  |  |  |  |  |  |  | P27 | SCREW_01X03 | 2:mpt_0,5%2f3-2,54 | conn | CONN_01X03 | / | / | 56B60BDE
D |  |  |  |  |  |  |  |  |  |  |  |  |  | C16 | 10nF | Capacitors_SMD:C_0805_HandSoldering | device | C_Small | / | / | 56B60BE4
D |  |  |  |  |  |  |  |  |  |  |  |  |  | P34 | CONN_01X03 | Pin_Headers:Pin_Header_Straight_1x03 | conn | CONN_01X03 | / | / | 56B60BFF
D |  |  |  |  |  |  |  |  |  |  |  |  |  | P33 | SCREW_01X03 | 2:mpt_0,5%2f3-2,54 | conn | CONN_01X03 | / | / | 56B60C05
D |  |  |  |  |  |  |  |  |  |  |  |  |  | C19 | 10nF | Capacitors_SMD:C_0805_HandSoldering | device | C_Small | / | / | 56B60C0B
D |  |  |  |  |  |  |  |  |  |  |  |  |  | U1 | STM32F103VE | ok-ic-smd:LQFP100-14x14 | stm32 | STM32F103VE | / | / | 56B691D4
D |  |  |  |  |  |  |  |  |  |  |  |  |  | C3 | 100nF | Capacitors_SMD:C_0805_HandSoldering | device | C_Small | / | / | 56B6E391
D |  |  |  |  |  |  |  |  |  |  |  |  |  | L1 | BEAD | ok-smd-generic:1206 | device | INDUCTOR_SMALL | / | / | 56B70621
D |  |  |  |  |  |  |  |  |  |  |  |  |  | C8 | 10uF | ok-polcaps-panasonic:CP-PANASONIC-SMT_C | device | C_Small | / | / | 56B70DFB
D |  |  |  |  |  |  |  |  |  |  |  |  |  | C9 | 10nF | Capacitors_SMD:C_0805_HandSoldering | device | C_Small | / | / | 56B71088
D |  |  |  |  |  |  |  |  |  |  |  |  |  | C4 | 100nF | Capacitors_SMD:C_0805_HandSoldering | device | C_Small | / | / | 56B735DD
D |  |  |  |  |  |  |  |  |  |  |  |  |  | C5 | 100nF | Capacitors_SMD:C_0805_HandSoldering | device | C_Small | / | / | 56B736B8
D |  |  |  |  |  |  |  |  |  |  |  |  |  | C6 | 100nF | Capacitors_SMD:C_0805_HandSoldering | device | C_Small | / | / | 56B73796
D |  |  |  |  |  |  |  |  |  |  |  |  |  | C1 | 100nF | Capacitors_SMD:C_0805_HandSoldering | device | C_Small | / | / | 56B7396F
D |  |  |  |  |  |  |  |  |  |  |  |  |  | U2 | USBLC6-2 | ReST-Library:SOT32-6L | ReST-cache | USBLC6-2 | / | / | 56B8256D
D |  |  |  |  |  |  |  |  |  |  |  |  |  | C7 | 100nF | Capacitors_SMD:C_0805_HandSoldering | device | C_Small | / | / | 56B8B2A9
D |  |  |  |  |  |  |  |  |  |  |  |  |  | R2 | 22R | Resistors_SMD:R_0805_HandSoldering | device | R_Small | / | / | 56B8DF24
D |  |  |  |  |  |  |  |  |  |  |  |  |  | R3 | 22R | Resistors_SMD:R_0805_HandSoldering | device | R_Small | / | / | 56B8E055
D |  |  |  |  |  |  |  |  |  |  |  |  |  | C10 | 10uF | ok-polcaps-panasonic:CP-PANASONIC-SMT_C | device | C_Small | / | / | 56B94F07
D |  |  |  |  |  |  |  |  |  |  |  |  |  | C11 | 22uF | ok-polcaps-panasonic:CP-PANASONIC-SMT_D | device | C_Small | / | / | 56B95427
D |  |  |  |  |  |  |  |  |  |  |  |  |  | P9 | CONN_01X02 | 5mm-pitch-terminal:mkds_1,5-2 | conn | CONN_01X02 | / | / | 56B9811D
D |  |  |  |  |  |  |  |  |  |  |  |  |  | F1 | F_Small | ReST-Library:JEF-703C | device | F_Small | / | / | 56B9B504
D |  |  |  |  |  |  |  |  |  |  |  |  |  | P18 | CONN_02X04 | Pin_Headers:Pin_Header_Straight_2x04 | conn | CONN_02X04 | / | / | 56B9A67A
D |  |  |  |  |  |  |  |  |  |  |  |  |  | P21 | CONN_02X04 | Pin_Headers:Pin_Header_Straight_2x04 | conn | CONN_02X04 | / | / | 56B9A7C6
D |  |  |  |  |  |  |  |  |  |  |  |  |  | IC1 | AT24C128 | Housings_SOIC:SOIC-8_3.9x4.9mm_Pitch1.27mm | ok-ic-atmel | AT24C256 | / | / | 56C3AD82
D |  |  |  |  |  |  |  |  |  |  |  |  |  | P3 | CONN_02X07 | Pin_Headers:Pin_Header_Angled_2x07 | conn | CONN_02X07 | / | / | 56CA1C17
D |  |  |  |  |  |  |  |  |  |  |  |  |  | P15 | CONN_01X05 | Pin_Headers:Pin_Header_Straight_1x05 | conn | CONN_01X05 | / | / | 56CDF755
D |  |  |  |  |  |  |  |  |  |  |  |  |  | P17 | CONN_01X04 | Pin_Headers:Pin_Header_Straight_1x04 | conn | CONN_01X04 | / | / | 56CEF795
D |  |  |  |  |  |  |  |  |  |  |  |  |  | P19 | CONN_01X04 | Pin_Headers:Pin_Header_Straight_1x04 | conn | CONN_01X04 | / | / | 56CF54CA
D |  |  |  |  |  |  |  |  |  |  |  |  |  | P10 | CONN_01X04 | Pin_Headers:Pin_Header_Straight_1x04 | conn | CONN_01X04 | / | / | 56CF969A
D |  |  |  |  |  |  |  |  |  |  |  |  |  | P6 | CONN_02X05 | Pin_Headers:Pin_Header_Straight_2x05 | conn | CONN_02X05 | / | / | 56D0A9CC
D |  |  |  |  |  |  |  |  |  |  |  |  |  | P7 | CONN_02X05 | Pin_Headers:Pin_Header_Straight_2x05 | conn | CONN_02X05 | / | / | 56D0B53C
D |  |  |  |  |  |  |  |  |  |  |  |  |  | R4 | 47R | Resistors_SMD:R_0805_HandSoldering | device | R_Small | / | / | 56D234EB
D |  |  |  |  |  |  |  |  |  |  |  |  |  | SW1 | SW-SPST-NO | Buttons_Switches_ThroughHole:SW_PUSH_SMALL | ok-switches | SW-SPST-NO | / | / | 56CABD63
D |  |  |  |  |  |  |  |  |  |  |  |  |  | R5 | 10K | Resistors_SMD:R_0805_HandSoldering | device | R_Small | / | / | 56CAD8A7
D |  |  |  |  |  |  |  |  |  |  |  |  |  | C2 | 100nF | Resistors_SMD:R_0805_HandSoldering | device | C_Small | / | / | 56CB1319
D |  |  |  |  |  |  |  |  |  |  |  |  |  | U4 | LM2574N-ADJ | Housings_DIP:DIP-8_W7.62mm_LongPads | dc-dc | LM2574N-ADJ | / | / | 56CBF5F6
D |  |  |  |  |  |  |  |  |  |  |  |  |  | L2 | 330uH | Inductors:SELF-WE-PD-XXL | device | INDUCTOR_SMALL | / | / | 56CC5991
D |  |  |  |  |  |  |  |  |  |  |  |  |  | D1 | 1N5819 | ReST-Library:DO-214AC(SMA) | device | D_Schottky_Small | / | / | 56CC5A96
D |  |  |  |  |  |  |  |  |  |  |  |  |  | C12 | 22uF | ok-polcaps-panasonic:CP-PANASONIC-SMT_D | device | C_Small | / | / | 56CC6900
D |  |  |  |  |  |  |  |  |  |  |  |  |  | R6 | 2K7 | Resistors_SMD:R_0805_HandSoldering | device | R_Small | / | / | 56CC6FF6
D |  |  |  |  |  |  |  |  |  |  |  |  |  | C13 | 220uF | ok-polcaps-panasonic:CP-PANASONIC-SMT_D | device | C_Small | / | / | 56CD3F54
D |  |  |  |  |  |  |  |  |  |  |  |  |  | R7 | 1K6 | Resistors_SMD:R_0805_HandSoldering | device | R_Small | / | / | 56CD5BD7
D |  |  |  |  |  |  |  |  |  |  |  |  |  | R1 | 1M | Resistors_SMD:R_0805_HandSoldering | device | R_Small | / | / | 56D13C58
D |  |  |  |  |  |  |  |  |  |  |  |  |  | P22 | CONN_01X03 | Pin_Headers:Pin_Header_Straight_1x03 | conn | CONN_01X03 | / | / | 56D2064A
D |  |  |  |  |  |  |  |  |  |  |  |  |  | P16 | CONN_01X03 | Pin_Headers:Pin_Header_Straight_1x03 | conn | CONN_01X03 | / | / | 56CC6E45
D |  |  |  |  |  |  |  |  |  |  |  |  |  | P13 | CONN_01X03 | Pin_Headers:Pin_Header_Straight_1x03 | conn | CONN_01X03 | / | / | 56CC6FE5
D |  |  |  |  |  |  |  |  |  |  |  |  |  | P5 | USB_OTG | Connect:USB_Mini-B | conn | USB_OTG | / | / | 56B80B48
D |  |  |  |  |  |  |  |  |  |  |  |  |  | P4 | CONN_02X10 | Pin_Headers:Pin_Header_Angled_2x10 | conn | CONN_02X10 | / | / | 56CEBD2E
D |  |  |  |  |  |  |  |  |  |  |  |  |  | P12 | CONN_02X04 | Pin_Headers:Pin_Header_Straight_2x04 | conn | CONN_02X04 | / | / | 56CF6A88
D |  |  |  |  |  |  |  |  |  |  |  |  |  | P11 | CONN_01X04 | Pin_Headers:Pin_Header_Straight_1x04 | conn | CONN_01X04 | / | / | 56CF726B
D |  |  |  |  |  |  |  |  |  |  |  |  |  | P2 | CONN_02X08 | Pin_Headers:Pin_Header_Angled_2x08 | conn | CONN_02X08 | / | / | 56CFCAC6
D |  |  |  |  |  |  |  |  |  |  |  |  |  | P1 | CONN_02X08 | Pin_Headers:Pin_Header_Angled_2x08 | conn | CONN_02X08 | / | / | 56D03E75
D |  |  |  |  |  |  |  |  |  |  |  |  |  | P8 | CONN_01X09 | Pin_Headers:Pin_Header_Straight_1x09 | conn | CONN_01X09 | / | / | 56D0A763
D |  |  |  |  |  |  |  |  |  |  |  |  |  | P14 | CONN_02X03 | Pin_Headers:Pin_Header_Straight_2x03 | conn | CONN_02X03 | / | / | 56D0CAB6
D |  |  |  |  |  |  |  |  |  |  |  |  |  | P40 | CONN_01X04 | Pin_Headers:Pin_Header_Straight_1x04 | conn | CONN_01X04 | / | / | 56D21C54
D |  |  |  |  |  |  |  |  |  |  |  |  |  | P41 | CONN_01X04 | Pin_Headers:Pin_Header_Straight_1x04 | conn | CONN_01X04 | / | / | 56D23585
D |  |  |  |  |  |  |  |  |  |  |  |  |  | P42 | CONN_01X04 | Pin_Headers:Pin_Header_Straight_1x04 | conn | CONN_01X04 | / | / | 56D23847
D |  |  |  |  |  |  |  |  |  |  |  |  |  | U3 | L7805ACD2T-TR | TO_SOT_Packages_SMD:SOT-404 | regul | LM117H | / | / | 56D0605D
D |  |  |  |  |  |  |  |  |  |  |  |  |  | R12 | 4K7 | Resistors_SMD:R_0805_HandSoldering | device | R_Small | / | / | 56D29E83
D |  |  |  |  |  |  |  |  |  |  |  |  |  | R13 | 4K7 | Resistors_SMD:R_0805_HandSoldering | device | R_Small | / | / | 56D2B222
D |  |  |  |  |  |  |  |  |  |  |  |  |  |  |  |  |  |  |  |  |  |  |  |  |  |  |  |  |  |  |  |  |  |  | 41 | GND | C12 | 2
D |  |  |  |  |  |  |  |  |  |  |  |  |  |  |  |  |  |  |  |  |  |  |  |  |  |  |  |  |  |  |  |  |  |  | 41 | GND | D1 | 2
D |  |  |  |  |  |  |  |  |  |  |  |  |  |  |  |  |  |  |  |  |  |  |  |  |  |  |  |  |  |  |  |  |  |  | 41 | GND | U4 | 4
D |  |  |  |  |  |  |  |  |  |  |  |  |  |  |  |  |  |  |  |  |  |  |  |  |  |  |  |  |  |  |  |  |  |  | 41 | GND | U4 | 3
D |  |  |  |  |  |  |  |  |  |  |  |  |  |  |  |  |  |  |  |  |  |  |  |  |  |  |  |  |  |  |  |  |  |  | 41 | GND | P10 | 4
D |  |  |  |  |  |  |  |  |  |  |  |  |  |  |  |  |  |  |  |  |  |  |  |  |  |  |  |  |  |  |  |  |  |  | 41 | GND | P19 | 4
D |  |  |  |  |  |  |  |  |  |  |  |  |  |  |  |  |  |  |  |  |  |  |  |  |  |  |  |  |  |  |  |  |  |  | 41 | GND | IC1 | 1
D |  |  |  |  |  |  |  |  |  |  |  |  |  |  |  |  |  |  |  |  |  |  |  |  |  |  |  |  |  |  |  |  |  |  | 41 | GND | P3 | 4
D |  |  |  |  |  |  |  |  |  |  |  |  |  |  |  |  |  |  |  |  |  |  |  |  |  |  |  |  |  |  |  |  |  |  | 41 | GND | P17 | 2
D |  |  |  |  |  |  |  |  |  |  |  |  |  |  |  |  |  |  |  |  |  |  |  |  |  |  |  |  |  |  |  |  |  |  | 41 | GND | P15 | 1
D |  |  |  |  |  |  |  |  |  |  |  |  |  |  |  |  |  |  |  |  |  |  |  |  |  |  |  |  |  |  |  |  |  |  | 41 | GND | P3 | 10
D |  |  |  |  |  |  |  |  |  |  |  |  |  |  |  |  |  |  |  |  |  |  |  |  |  |  |  |  |  |  |  |  |  |  | 41 | GND | P3 | 8
D |  |  |  |  |  |  |  |  |  |  |  |  |  |  |  |  |  |  |  |  |  |  |  |  |  |  |  |  |  |  |  |  |  |  | 41 | GND | P3 | 6
D |  |  |  |  |  |  |  |  |  |  |  |  |  |  |  |  |  |  |  |  |  |  |  |  |  |  |  |  |  |  |  |  |  |  | 41 | GND | P6 | 1
D |  |  |  |  |  |  |  |  |  |  |  |  |  |  |  |  |  |  |  |  |  |  |  |  |  |  |  |  |  |  |  |  |  |  | 41 | GND | P3 | 2
D |  |  |  |  |  |  |  |  |  |  |  |  |  |  |  |  |  |  |  |  |  |  |  |  |  |  |  |  |  |  |  |  |  |  | 41 | GND | IC1 | 7
D |  |  |  |  |  |  |  |  |  |  |  |  |  |  |  |  |  |  |  |  |  |  |  |  |  |  |  |  |  |  |  |  |  |  | 41 | GND | IC1 | 4
D |  |  |  |  |  |  |  |  |  |  |  |  |  |  |  |  |  |  |  |  |  |  |  |  |  |  |  |  |  |  |  |  |  |  | 41 | GND | IC1 | 2
D |  |  |  |  |  |  |  |  |  |  |  |  |  |  |  |  |  |  |  |  |  |  |  |  |  |  |  |  |  |  |  |  |  |  | 41 | GND | C2 | 1
D |  |  |  |  |  |  |  |  |  |  |  |  |  |  |  |  |  |  |  |  |  |  |  |  |  |  |  |  |  |  |  |  |  |  | 41 | GND | P18 | 8
D |  |  |  |  |  |  |  |  |  |  |  |  |  |  |  |  |  |  |  |  |  |  |  |  |  |  |  |  |  |  |  |  |  |  | 41 | GND | C3 | 2
D |  |  |  |  |  |  |  |  |  |  |  |  |  |  |  |  |  |  |  |  |  |  |  |  |  |  |  |  |  |  |  |  |  |  | 41 | GND | U1 | 99
D |  |  |  |  |  |  |  |  |  |  |  |  |  |  |  |  |  |  |  |  |  |  |  |  |  |  |  |  |  |  |  |  |  |  | 41 | GND | U1 | 49
D |  |  |  |  |  |  |  |  |  |  |  |  |  |  |  |  |  |  |  |  |  |  |  |  |  |  |  |  |  |  |  |  |  |  | 41 | GND | P9 | 2
D |  |  |  |  |  |  |  |  |  |  |  |  |  |  |  |  |  |  |  |  |  |  |  |  |  |  |  |  |  |  |  |  |  |  | 41 | GND | U1 | 19
D |  |  |  |  |  |  |  |  |  |  |  |  |  |  |  |  |  |  |  |  |  |  |  |  |  |  |  |  |  |  |  |  |  |  | 41 | GND | P18 | 4
D |  |  |  |  |  |  |  |  |  |  |  |  |  |  |  |  |  |  |  |  |  |  |  |  |  |  |  |  |  |  |  |  |  |  | 41 | GND | U1 | 27
D |  |  |  |  |  |  |  |  |  |  |  |  |  |  |  |  |  |  |  |  |  |  |  |  |  |  |  |  |  |  |  |  |  |  | 41 | GND | P18 | 6
D |  |  |  |  |  |  |  |  |  |  |  |  |  |  |  |  |  |  |  |  |  |  |  |  |  |  |  |  |  |  |  |  |  |  | 41 | GND | P18 | 2
D |  |  |  |  |  |  |  |  |  |  |  |  |  |  |  |  |  |  |  |  |  |  |  |  |  |  |  |  |  |  |  |  |  |  | 41 | GND | C9 | 2
D |  |  |  |  |  |  |  |  |  |  |  |  |  |  |  |  |  |  |  |  |  |  |  |  |  |  |  |  |  |  |  |  |  |  | 41 | GND | C1 | 2
D |  |  |  |  |  |  |  |  |  |  |  |  |  |  |  |  |  |  |  |  |  |  |  |  |  |  |  |  |  |  |  |  |  |  | 41 | GND | C6 | 2
D |  |  |  |  |  |  |  |  |  |  |  |  |  |  |  |  |  |  |  |  |  |  |  |  |  |  |  |  |  |  |  |  |  |  | 41 | GND | C5 | 2
D |  |  |  |  |  |  |  |  |  |  |  |  |  |  |  |  |  |  |  |  |  |  |  |  |  |  |  |  |  |  |  |  |  |  | 41 | GND | U2 | 2
D |  |  |  |  |  |  |  |  |  |  |  |  |  |  |  |  |  |  |  |  |  |  |  |  |  |  |  |  |  |  |  |  |  |  | 41 | GND | C4 | 2
D |  |  |  |  |  |  |  |  |  |  |  |  |  |  |  |  |  |  |  |  |  |  |  |  |  |  |  |  |  |  |  |  |  |  | 41 | GND | U6 | 7
D |  |  |  |  |  |  |  |  |  |  |  |  |  |  |  |  |  |  |  |  |  |  |  |  |  |  |  |  |  |  |  |  |  |  | 41 | GND | C8 | 2
D |  |  |  |  |  |  |  |  |  |  |  |  |  |  |  |  |  |  |  |  |  |  |  |  |  |  |  |  |  |  |  |  |  |  | 41 | GND | C11 | 1
D |  |  |  |  |  |  |  |  |  |  |  |  |  |  |  |  |  |  |  |  |  |  |  |  |  |  |  |  |  |  |  |  |  |  | 41 | GND | C10 | 1
D |  |  |  |  |  |  |  |  |  |  |  |  |  |  |  |  |  |  |  |  |  |  |  |  |  |  |  |  |  |  |  |  |  |  | 41 | GND | C7 | 2
D |  |  |  |  |  |  |  |  |  |  |  |  |  |  |  |  |  |  |  |  |  |  |  |  |  |  |  |  |  |  |  |  |  |  | 41 | GND | C19 | 2
D |  |  |  |  |  |  |  |  |  |  |  |  |  |  |  |  |  |  |  |  |  |  |  |  |  |  |  |  |  |  |  |  |  |  | 41 | GND | P33 | 2
D |  |  |  |  |  |  |  |  |  |  |  |  |  |  |  |  |  |  |  |  |  |  |  |  |  |  |  |  |  |  |  |  |  |  | 41 | GND | P34 | 2
D |  |  |  |  |  |  |  |  |  |  |  |  |  |  |  |  |  |  |  |  |  |  |  |  |  |  |  |  |  |  |  |  |  |  | 41 | GND | C16 | 2
D |  |  |  |  |  |  |  |  |  |  |  |  |  |  |  |  |  |  |  |  |  |  |  |  |  |  |  |  |  |  |  |  |  |  | 41 | GND | P24 | 2
D |  |  |  |  |  |  |  |  |  |  |  |  |  |  |  |  |  |  |  |  |  |  |  |  |  |  |  |  |  |  |  |  |  |  | 41 | GND | U5 | 7
D |  |  |  |  |  |  |  |  |  |  |  |  |  |  |  |  |  |  |  |  |  |  |  |  |  |  |  |  |  |  |  |  |  |  | 41 | GND | P28 | 2
D |  |  |  |  |  |  |  |  |  |  |  |  |  |  |  |  |  |  |  |  |  |  |  |  |  |  |  |  |  |  |  |  |  |  | 41 | GND | C22 | 2
D |  |  |  |  |  |  |  |  |  |  |  |  |  |  |  |  |  |  |  |  |  |  |  |  |  |  |  |  |  |  |  |  |  |  | 41 | GND | U8 | 7
D |  |  |  |  |  |  |  |  |  |  |  |  |  |  |  |  |  |  |  |  |  |  |  |  |  |  |  |  |  |  |  |  |  |  | 41 | GND | U8 | 1
D |  |  |  |  |  |  |  |  |  |  |  |  |  |  |  |  |  |  |  |  |  |  |  |  |  |  |  |  |  |  |  |  |  |  | 41 | GND | U1 | 20
D |  |  |  |  |  |  |  |  |  |  |  |  |  |  |  |  |  |  |  |  |  |  |  |  |  |  |  |  |  |  |  |  |  |  | 41 | GND | U1 | 10
D |  |  |  |  |  |  |  |  |  |  |  |  |  |  |  |  |  |  |  |  |  |  |  |  |  |  |  |  |  |  |  |  |  |  | 41 | GND | U1 | 74
D |  |  |  |  |  |  |  |  |  |  |  |  |  |  |  |  |  |  |  |  |  |  |  |  |  |  |  |  |  |  |  |  |  |  | 41 | GND | P27 | 2
D |  |  |  |  |  |  |  |  |  |  |  |  |  |  |  |  |  |  |  |  |  |  |  |  |  |  |  |  |  |  |  |  |  |  | 41 | GND | R8 | 2
D |  |  |  |  |  |  |  |  |  |  |  |  |  |  |  |  |  |  |  |  |  |  |  |  |  |  |  |  |  |  |  |  |  |  | 41 | GND | C18 | 2
D |  |  |  |  |  |  |  |  |  |  |  |  |  |  |  |  |  |  |  |  |  |  |  |  |  |  |  |  |  |  |  |  |  |  | 41 | GND | P31 | 2
D |  |  |  |  |  |  |  |  |  |  |  |  |  |  |  |  |  |  |  |  |  |  |  |  |  |  |  |  |  |  |  |  |  |  | 41 | GND | P32 | 2
D |  |  |  |  |  |  |  |  |  |  |  |  |  |  |  |  |  |  |  |  |  |  |  |  |  |  |  |  |  |  |  |  |  |  | 41 | GND | C15 | 2
D |  |  |  |  |  |  |  |  |  |  |  |  |  |  |  |  |  |  |  |  |  |  |  |  |  |  |  |  |  |  |  |  |  |  | 41 | GND | U7 | 1
D |  |  |  |  |  |  |  |  |  |  |  |  |  |  |  |  |  |  |  |  |  |  |  |  |  |  |  |  |  |  |  |  |  |  | 41 | GND | R9 | 2
D |  |  |  |  |  |  |  |  |  |  |  |  |  |  |  |  |  |  |  |  |  |  |  |  |  |  |  |  |  |  |  |  |  |  | 41 | GND | C21 | 2
D |  |  |  |  |  |  |  |  |  |  |  |  |  |  |  |  |  |  |  |  |  |  |  |  |  |  |  |  |  |  |  |  |  |  | 41 | GND | U7 | 7
D |  |  |  |  |  |  |  |  |  |  |  |  |  |  |  |  |  |  |  |  |  |  |  |  |  |  |  |  |  |  |  |  |  |  | 41 | GND | U6 | 1
D |  |  |  |  |  |  |  |  |  |  |  |  |  |  |  |  |  |  |  |  |  |  |  |  |  |  |  |  |  |  |  |  |  |  | 41 | GND | C20 | 2
D |  |  |  |  |  |  |  |  |  |  |  |  |  |  |  |  |  |  |  |  |  |  |  |  |  |  |  |  |  |  |  |  |  |  | 41 | GND | C14 | 2
D |  |  |  |  |  |  |  |  |  |  |  |  |  |  |  |  |  |  |  |  |  |  |  |  |  |  |  |  |  |  |  |  |  |  | 41 | GND | P23 | 2
D |  |  |  |  |  |  |  |  |  |  |  |  |  |  |  |  |  |  |  |  |  |  |  |  |  |  |  |  |  |  |  |  |  |  | 41 | GND | P20 | 2
D |  |  |  |  |  |  |  |  |  |  |  |  |  |  |  |  |  |  |  |  |  |  |  |  |  |  |  |  |  |  |  |  |  |  | 41 | GND | P20 | 1
D |  |  |  |  |  |  |  |  |  |  |  |  |  |  |  |  |  |  |  |  |  |  |  |  |  |  |  |  |  |  |  |  |  |  | 41 | GND | X1 | 3
D |  |  |  |  |  |  |  |  |  |  |  |  |  |  |  |  |  |  |  |  |  |  |  |  |  |  |  |  |  |  |  |  |  |  | 41 | GND | U5 | 1
D |  |  |  |  |  |  |  |  |  |  |  |  |  |  |  |  |  |  |  |  |  |  |  |  |  |  |  |  |  |  |  |  |  |  | 41 | GND | P2 | 16
D |  |  |  |  |  |  |  |  |  |  |  |  |  |  |  |  |  |  |  |  |  |  |  |  |  |  |  |  |  |  |  |  |  |  | 41 | GND | P2 | 15
D |  |  |  |  |  |  |  |  |  |  |  |  |  |  |  |  |  |  |  |  |  |  |  |  |  |  |  |  |  |  |  |  |  |  | 41 | GND | P1 | 15
D |  |  |  |  |  |  |  |  |  |  |  |  |  |  |  |  |  |  |  |  |  |  |  |  |  |  |  |  |  |  |  |  |  |  | 41 | GND | P8 | 7
D |  |  |  |  |  |  |  |  |  |  |  |  |  |  |  |  |  |  |  |  |  |  |  |  |  |  |  |  |  |  |  |  |  |  | 41 | GND | P1 | 16
D |  |  |  |  |  |  |  |  |  |  |  |  |  |  |  |  |  |  |  |  |  |  |  |  |  |  |  |  |  |  |  |  |  |  | 41 | GND | P1 | 6
D |  |  |  |  |  |  |  |  |  |  |  |  |  |  |  |  |  |  |  |  |  |  |  |  |  |  |  |  |  |  |  |  |  |  | 41 | GND | P1 | 4
D |  |  |  |  |  |  |  |  |  |  |  |  |  |  |  |  |  |  |  |  |  |  |  |  |  |  |  |  |  |  |  |  |  |  | 41 | GND | U3 | 2
D |  |  |  |  |  |  |  |  |  |  |  |  |  |  |  |  |  |  |  |  |  |  |  |  |  |  |  |  |  |  |  |  |  |  | 41 | GND | P14 | 6
D |  |  |  |  |  |  |  |  |  |  |  |  |  |  |  |  |  |  |  |  |  |  |  |  |  |  |  |  |  |  |  |  |  |  | 41 | GND | P14 | 5
D |  |  |  |  |  |  |  |  |  |  |  |  |  |  |  |  |  |  |  |  |  |  |  |  |  |  |  |  |  |  |  |  |  |  | 41 | GND | P1 | 2
D |  |  |  |  |  |  |  |  |  |  |  |  |  |  |  |  |  |  |  |  |  |  |  |  |  |  |  |  |  |  |  |  |  |  | 41 | GND | R7 | 2
D |  |  |  |  |  |  |  |  |  |  |  |  |  |  |  |  |  |  |  |  |  |  |  |  |  |  |  |  |  |  |  |  |  |  | 41 | GND | P12 | 4
D |  |  |  |  |  |  |  |  |  |  |  |  |  |  |  |  |  |  |  |  |  |  |  |  |  |  |  |  |  |  |  |  |  |  | 41 | GND | P4 | 6
D |  |  |  |  |  |  |  |  |  |  |  |  |  |  |  |  |  |  |  |  |  |  |  |  |  |  |  |  |  |  |  |  |  |  | 41 | GND | P4 | 4
D |  |  |  |  |  |  |  |  |  |  |  |  |  |  |  |  |  |  |  |  |  |  |  |  |  |  |  |  |  |  |  |  |  |  | 41 | GND | P4 | 2
D |  |  |  |  |  |  |  |  |  |  |  |  |  |  |  |  |  |  |  |  |  |  |  |  |  |  |  |  |  |  |  |  |  |  | 41 | GND | P5 | 5
D |  |  |  |  |  |  |  |  |  |  |  |  |  |  |  |  |  |  |  |  |  |  |  |  |  |  |  |  |  |  |  |  |  |  | 41 | GND | P2 | 6
D |  |  |  |  |  |  |  |  |  |  |  |  |  |  |  |  |  |  |  |  |  |  |  |  |  |  |  |  |  |  |  |  |  |  | 41 | GND | P2 | 4
D |  |  |  |  |  |  |  |  |  |  |  |  |  |  |  |  |  |  |  |  |  |  |  |  |  |  |  |  |  |  |  |  |  |  | 41 | GND | P2 | 2
D |  |  |  |  |  |  |  |  |  |  |  |  |  |  |  |  |  |  |  |  |  |  |  |  |  |  |  |  |  |  |  |  |  |  | 41 | GND | P12 | 8
D |  |  |  |  |  |  |  |  |  |  |  |  |  |  |  |  |  |  |  |  |  |  |  |  |  |  |  |  |  |  |  |  |  |  | 41 | GND | P12 | 6
D |  |  |  |  |  |  |  |  |  |  |  |  |  |  |  |  |  |  |  |  |  |  |  |  |  |  |  |  |  |  |  |  |  |  | 41 | GND | P4 | 8
D |  |  |  |  |  |  |  |  |  |  |  |  |  |  |  |  |  |  |  |  |  |  |  |  |  |  |  |  |  |  |  |  |  |  | 41 | GND | P12 | 2
D |  |  |  |  |  |  |  |  |  |  |  |  |  |  |  |  |  |  |  |  |  |  |  |  |  |  |  |  |  |  |  |  |  |  | 41 | GND | R1 | 1
D |  |  |  |  |  |  |  |  |  |  |  |  |  |  |  |  |  |  |  |  |  |  |  |  |  |  |  |  |  |  |  |  |  |  | 41 | GND | P4 | 10
D |  |  |  |  |  |  |  |  |  |  |  |  |  |  |  |  |  |  |  |  |  |  |  |  |  |  |  |  |  |  |  |  |  |  | 41 | GND | P4 | 13
D |  |  |  |  |  |  |  |  |  |  |  |  |  |  |  |  |  |  |  |  |  |  |  |  |  |  |  |  |  |  |  |  |  |  | 41 | GND | P4 | 12
D |  |  |  |  |  |  |  |  |  |  |  |  |  |  |  |  |  |  |  |  |  |  |  |  |  |  |  |  |  |  |  |  |  |  | 42 | /E1-DIR | U1 | 18
D |  |  |  |  |  |  |  |  |  |  |  |  |  |  |  |  |  |  |  |  |  |  |  |  |  |  |  |  |  |  |  |  |  |  | 42 | /E1-DIR | P4 | 20
D |  |  |  |  |  |  |  |  |  |  |  |  |  |  |  |  |  |  |  |  |  |  |  |  |  |  |  |  |  |  |  |  |  |  | 43 | Net-(P5-Pad4) | P5 | 4
D |  |  |  |  |  |  |  |  |  |  |  |  |  |  |  |  |  |  |  |  |  |  |  |  |  |  |  |  |  |  |  |  |  |  | 44 | Net-(P5-Pad6) | P5 | 6
D |  |  |  |  |  |  |  |  |  |  |  |  |  |  |  |  |  |  |  |  |  |  |  |  |  |  |  |  |  |  |  |  |  |  | 44 | Net-(P5-Pad6) | R1 | 2
D |  |  |  |  |  |  |  |  |  |  |  |  |  |  |  |  |  |  |  |  |  |  |  |  |  |  |  |  |  |  |  |  |  |  | 45 | VREF | R4 | 2
D |  |  |  |  |  |  |  |  |  |  |  |  |  |  |  |  |  |  |  |  |  |  |  |  |  |  |  |  |  |  |  |  |  |  | 45 | VREF | U1 | 22
D |  |  |  |  |  |  |  |  |  |  |  |  |  |  |  |  |  |  |  |  |  |  |  |  |  |  |  |  |  |  |  |  |  |  | 45 | VREF | C8 | 1
D |  |  |  |  |  |  |  |  |  |  |  |  |  |  |  |  |  |  |  |  |  |  |  |  |  |  |  |  |  |  |  |  |  |  | 45 | VREF | L1 | 2
D |  |  |  |  |  |  |  |  |  |  |  |  |  |  |  |  |  |  |  |  |  |  |  |  |  |  |  |  |  |  |  |  |  |  | 45 | VREF | C9 | 1
D |  |  |  |  |  |  |  |  |  |  |  |  |  |  |  |  |  |  |  |  |  |  |  |  |  |  |  |  |  |  |  |  |  |  | 46 | Net-(U1-Pad6) | U1 | 6
D |  |  |  |  |  |  |  |  |  |  |  |  |  |  |  |  |  |  |  |  |  |  |  |  |  |  |  |  |  |  |  |  |  |  | 47 | Net-(P5-Pad2) | U2 | 1
D |  |  |  |  |  |  |  |  |  |  |  |  |  |  |  |  |  |  |  |  |  |  |  |  |  |  |  |  |  |  |  |  |  |  | 47 | Net-(P5-Pad2) | P5 | 2
D |  |  |  |  |  |  |  |  |  |  |  |  |  |  |  |  |  |  |  |  |  |  |  |  |  |  |  |  |  |  |  |  |  |  | 48 | VAA | C12 | 1
D |  |  |  |  |  |  |  |  |  |  |  |  |  |  |  |  |  |  |  |  |  |  |  |  |  |  |  |  |  |  |  |  |  |  | 48 | VAA | U4 | 5
D |  |  |  |  |  |  |  |  |  |  |  |  |  |  |  |  |  |  |  |  |  |  |  |  |  |  |  |  |  |  |  |  |  |  | 48 | VAA | P13 | 2
D |  |  |  |  |  |  |  |  |  |  |  |  |  |  |  |  |  |  |  |  |  |  |  |  |  |  |  |  |  |  |  |  |  |  | 49 | VCC/2 | P16 | 3
D |  |  |  |  |  |  |  |  |  |  |  |  |  |  |  |  |  |  |  |  |  |  |  |  |  |  |  |  |  |  |  |  |  |  | 49 | VCC/2 | C11 | 2
D |  |  |  |  |  |  |  |  |  |  |  |  |  |  |  |  |  |  |  |  |  |  |  |  |  |  |  |  |  |  |  |  |  |  | 49 | VCC/2 | U3 | 3
D |  |  |  |  |  |  |  |  |  |  |  |  |  |  |  |  |  |  |  |  |  |  |  |  |  |  |  |  |  |  |  |  |  |  | 50 | VCC | P16 | 1
D |  |  |  |  |  |  |  |  |  |  |  |  |  |  |  |  |  |  |  |  |  |  |  |  |  |  |  |  |  |  |  |  |  |  | 50 | VCC | U2 | 5
D |  |  |  |  |  |  |  |  |  |  |  |  |  |  |  |  |  |  |  |  |  |  |  |  |  |  |  |  |  |  |  |  |  |  | 50 | VCC | C7 | 1
D |  |  |  |  |  |  |  |  |  |  |  |  |  |  |  |  |  |  |  |  |  |  |  |  |  |  |  |  |  |  |  |  |  |  | 50 | VCC | P5 | 1
D |  |  |  |  |  |  |  |  |  |  |  |  |  |  |  |  |  |  |  |  |  |  |  |  |  |  |  |  |  |  |  |  |  |  | 51 | Net-(P37-Pad2) | P41 | 2
D |  |  |  |  |  |  |  |  |  |  |  |  |  |  |  |  |  |  |  |  |  |  |  |  |  |  |  |  |  |  |  |  |  |  | 51 | Net-(P37-Pad2) | U6 | 5
D |  |  |  |  |  |  |  |  |  |  |  |  |  |  |  |  |  |  |  |  |  |  |  |  |  |  |  |  |  |  |  |  |  |  | 51 | Net-(P37-Pad2) | P37 | 2
D |  |  |  |  |  |  |  |  |  |  |  |  |  |  |  |  |  |  |  |  |  |  |  |  |  |  |  |  |  |  |  |  |  |  | 52 | Net-(U1-Pad12) | U1 | 12
D |  |  |  |  |  |  |  |  |  |  |  |  |  |  |  |  |  |  |  |  |  |  |  |  |  |  |  |  |  |  |  |  |  |  | 52 | Net-(U1-Pad12) | X1 | 1
D |  |  |  |  |  |  |  |  |  |  |  |  |  |  |  |  |  |  |  |  |  |  |  |  |  |  |  |  |  |  |  |  |  |  | 53 | Net-(U1-Pad13) | U1 | 13
D |  |  |  |  |  |  |  |  |  |  |  |  |  |  |  |  |  |  |  |  |  |  |  |  |  |  |  |  |  |  |  |  |  |  | 53 | Net-(U1-Pad13) | X1 | 2
D |  |  |  |  |  |  |  |  |  |  |  |  |  |  |  |  |  |  |  |  |  |  |  |  |  |  |  |  |  |  |  |  |  |  | 54 | Net-(P38-Pad4) | P38 | 4
D |  |  |  |  |  |  |  |  |  |  |  |  |  |  |  |  |  |  |  |  |  |  |  |  |  |  |  |  |  |  |  |  |  |  | 54 | Net-(P38-Pad4) | P42 | 4
D |  |  |  |  |  |  |  |  |  |  |  |  |  |  |  |  |  |  |  |  |  |  |  |  |  |  |  |  |  |  |  |  |  |  | 54 | Net-(P38-Pad4) | U8 | 3
D |  |  |  |  |  |  |  |  |  |  |  |  |  |  |  |  |  |  |  |  |  |  |  |  |  |  |  |  |  |  |  |  |  |  | 55 | Net-(P38-Pad3) | P42 | 3
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

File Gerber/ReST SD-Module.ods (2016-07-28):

ID | Bezeichner | GehÃ¤use | StÃ¼ckzahl | Bezeichnung | Anbieter | und | Ref.
3 | C1 | TantalC_SizeA_EIA-3216_HandSoldering | 1 | CP1_Small
4 | CON1,CON2 | SD_Card_Receptacle | 2 | uSD_Card
5 | D1 | LED_0805 | 1 | Led_Small
6 | P1 | Pin_Header_Straight_2x05 | 1 | CONN_02X05
7 | R2 | R_0805_HandSoldering | 1 | 1K
8 | U1 | SOT-23-5 | 1 | MIC5205

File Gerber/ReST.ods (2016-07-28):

ID | Bezeichner | GehÃ¤use | StÃ¼ckzahl | Bezeichnung | Anbieter und Ref.
2 | U9 | LQFP100-14x14 | 1 | STM32F10x/STM32F4x
3 | D2 | DO-214AC.SMA | 1 | B240A
4 | C1,C2,C3,C4,C5,C6 | C_0805_HandSoldering | 6 | 10nF
5 | C7,C8,C9,C13,C14 | CP-PANASONIC-SMT_D8 | 5 | 100uF
6 | C10 | C_1206_HandSoldering | 1 | 10uF
7 | C11 | C_0805_HandSoldering | 1 | 22nF
8 | C12,C26 | C_0805_HandSoldering | 2 | 4.7uF
9 | C15 | R_0805_HandSoldering | 1 | 100nF
10 | C16,C32,C33,C34,C35,C36,C37,C38,C39 | C_0805_HandSoldering | 9 | 10uF
11 | C17,C18 | R_0805_HandSoldering | 2 | 10pF
12 | C19,C20,C21,C22,C23,C24,C25,C29 | C_0805_HandSoldering | 8 | 100nF
13 | C27,C28 | C_0805_HandSoldering | 2 | 2u2
14 | D1,D3 | DO-214AC.SMA | 2 | 1N400x
15 | D4,D5,D10,D11,D12 | LED_0805 | 5 | LED
16 | D13,D14,D15 | DO-214AC.SMA | 3 | D_1N400x-SMD
17 | F1,F2 | MINI-FUSE | 2 | F_Small
18 | IC1 | SOIC-8_3.9x4.9mm_Pitch1.27mm | 1 | AT24C256
19 | L1 | C_0805_HandSoldering | 1 | BEAD
20 | L2 | CD32 | 1 | 4.7uH
21 | L3 | CD32 | 1 | 2.2uH
22 | P1,P3,P29,P30,P31 | screw-5-2P | 5 | CONN_01X02
23 | P2 | bb02-hy03a | 1 | CONN_01X03
24 | P4,P5,P6,P7,P8,P9 | Pin_Header_Straight_1x03 | 6 | CONN_01X03
25 | P10,P40 | Pin_Header_Straight_2x04 | 2 | CONN_02X04
26 | P11,P12,P13,P14,P21 | Pin_Header_Straight_1x04 | 5 | CONN_01X04
27 | P16,P17 | IDC_Header_Straight_10pins | 2 | CONN_02X05
28 | P18 | Pin_Header_Straight_2x05 | 1 | CONN_02X05
29 | P20 | Pin_Header_Straight_1x02 | 1 | CONN_01X02
30 | P22,P23,P35,P36,P37,P38,P39 | bb02-hp06 | 7 | CONN_02X03
31 | P25,P26 | Pin_Header_Straight_2x03 | 2 | CONN_02X03
32 | P27 | Pin_Header_Straight_2x06 | 1 | CONN_02X06
33 | P28,P32 | pt_1,5-4-3,5-h | 2 | CONN_02X02
34 | P33,P34 | Pin_Header_Straight_1x04 | 2 | CONN_02X02
35 | Q1,Q2,Q3,Q4 | SOT-23 | 4 | 2n7002
36 | Q7,Q8,Q9 | SOT-23 | 3 | Q_BSH105/IRLML2502
37 | Q10,Q11,Q12 | TO-220_Neutral123_Vertical_LargePads | 3 | Q_AOT240L
38 | R1,R2,R3,R4,R5 | R_0805_HandSoldering | 5 | 100K
39 | R6 | R_0805_HandSoldering | 1 | 28.7k
40 | R7 | R_0805_HandSoldering | 1 | 150K
41 | R8 | R_0805_HandSoldering | 1 | 10K
42 | R9 | R_0805_HandSoldering | 1 | 1M
43 | R10,R11,R29,R30,R31,R32,R33,R34 | R_0805_HandSoldering | 8 | 4K7
44 | R12,R13 | R_0805_HandSoldering | 2 | 22R
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

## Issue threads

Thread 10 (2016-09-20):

Vollfarb LCD Platine

berryelectronics, 2016-09-20:
Kompletten Bildschirm mit Treiber und SD Karte.
Vielleicht einen Extra Prozessor? -> Wie wird dieser geupdatet?

Großer Bildschirm. 3.5 Zoll ist vielleicht noch ein bisschen zu klein...

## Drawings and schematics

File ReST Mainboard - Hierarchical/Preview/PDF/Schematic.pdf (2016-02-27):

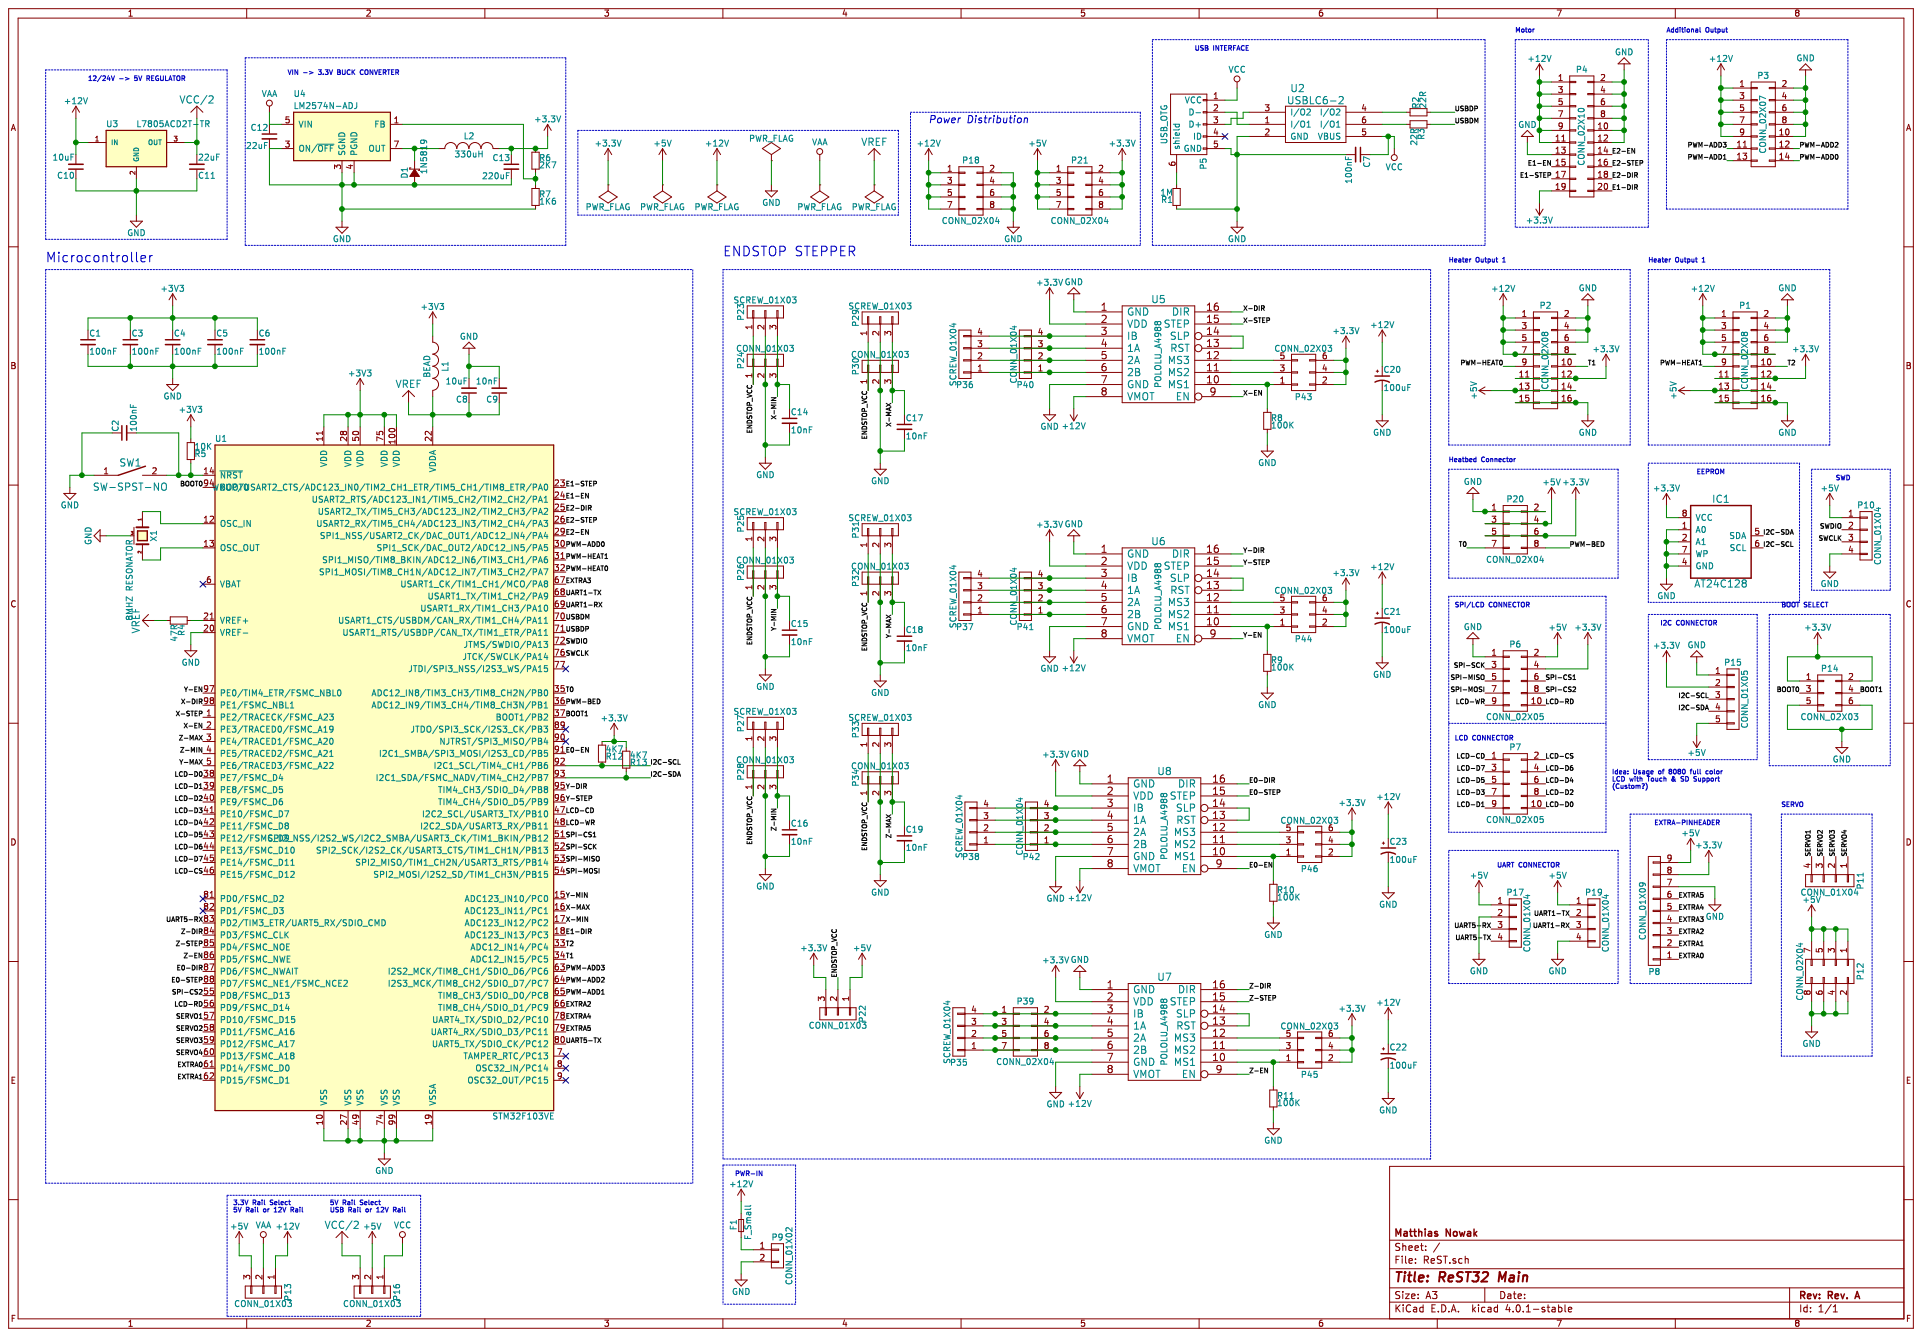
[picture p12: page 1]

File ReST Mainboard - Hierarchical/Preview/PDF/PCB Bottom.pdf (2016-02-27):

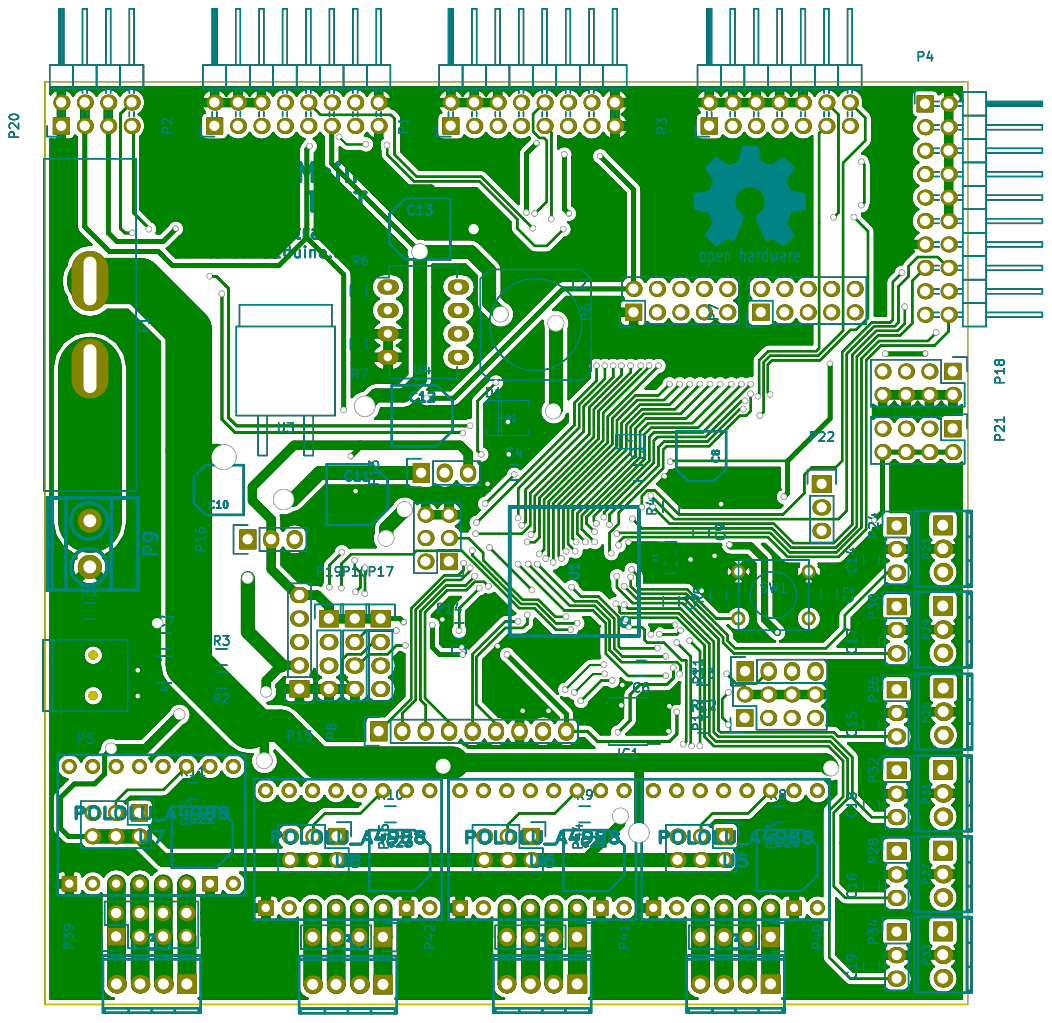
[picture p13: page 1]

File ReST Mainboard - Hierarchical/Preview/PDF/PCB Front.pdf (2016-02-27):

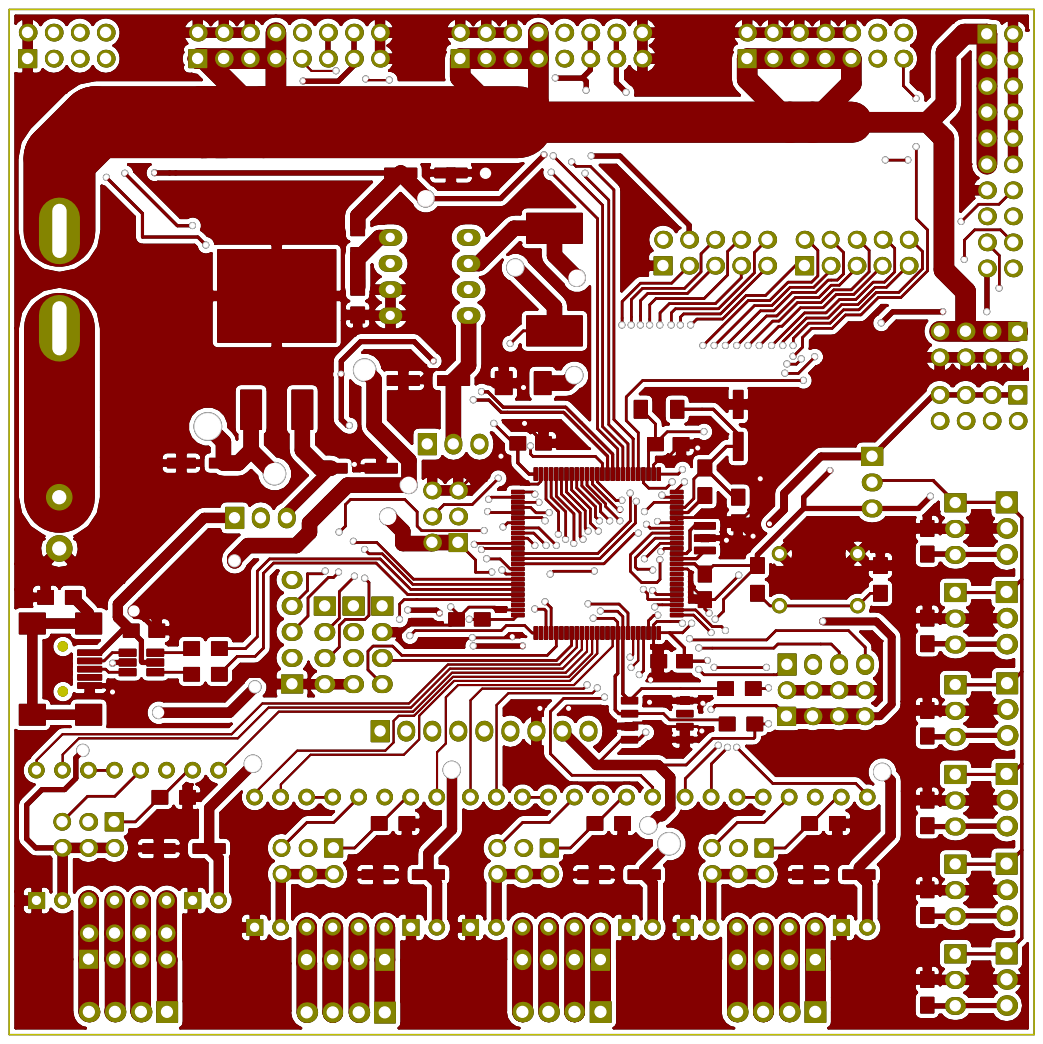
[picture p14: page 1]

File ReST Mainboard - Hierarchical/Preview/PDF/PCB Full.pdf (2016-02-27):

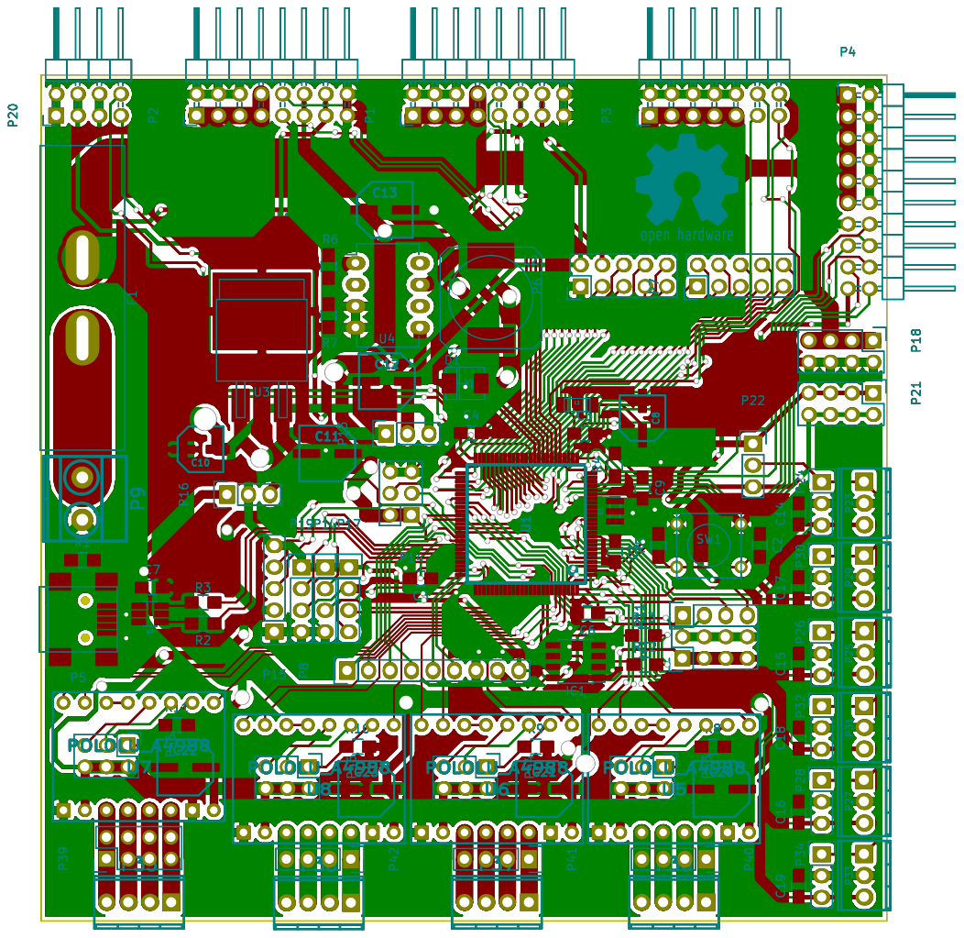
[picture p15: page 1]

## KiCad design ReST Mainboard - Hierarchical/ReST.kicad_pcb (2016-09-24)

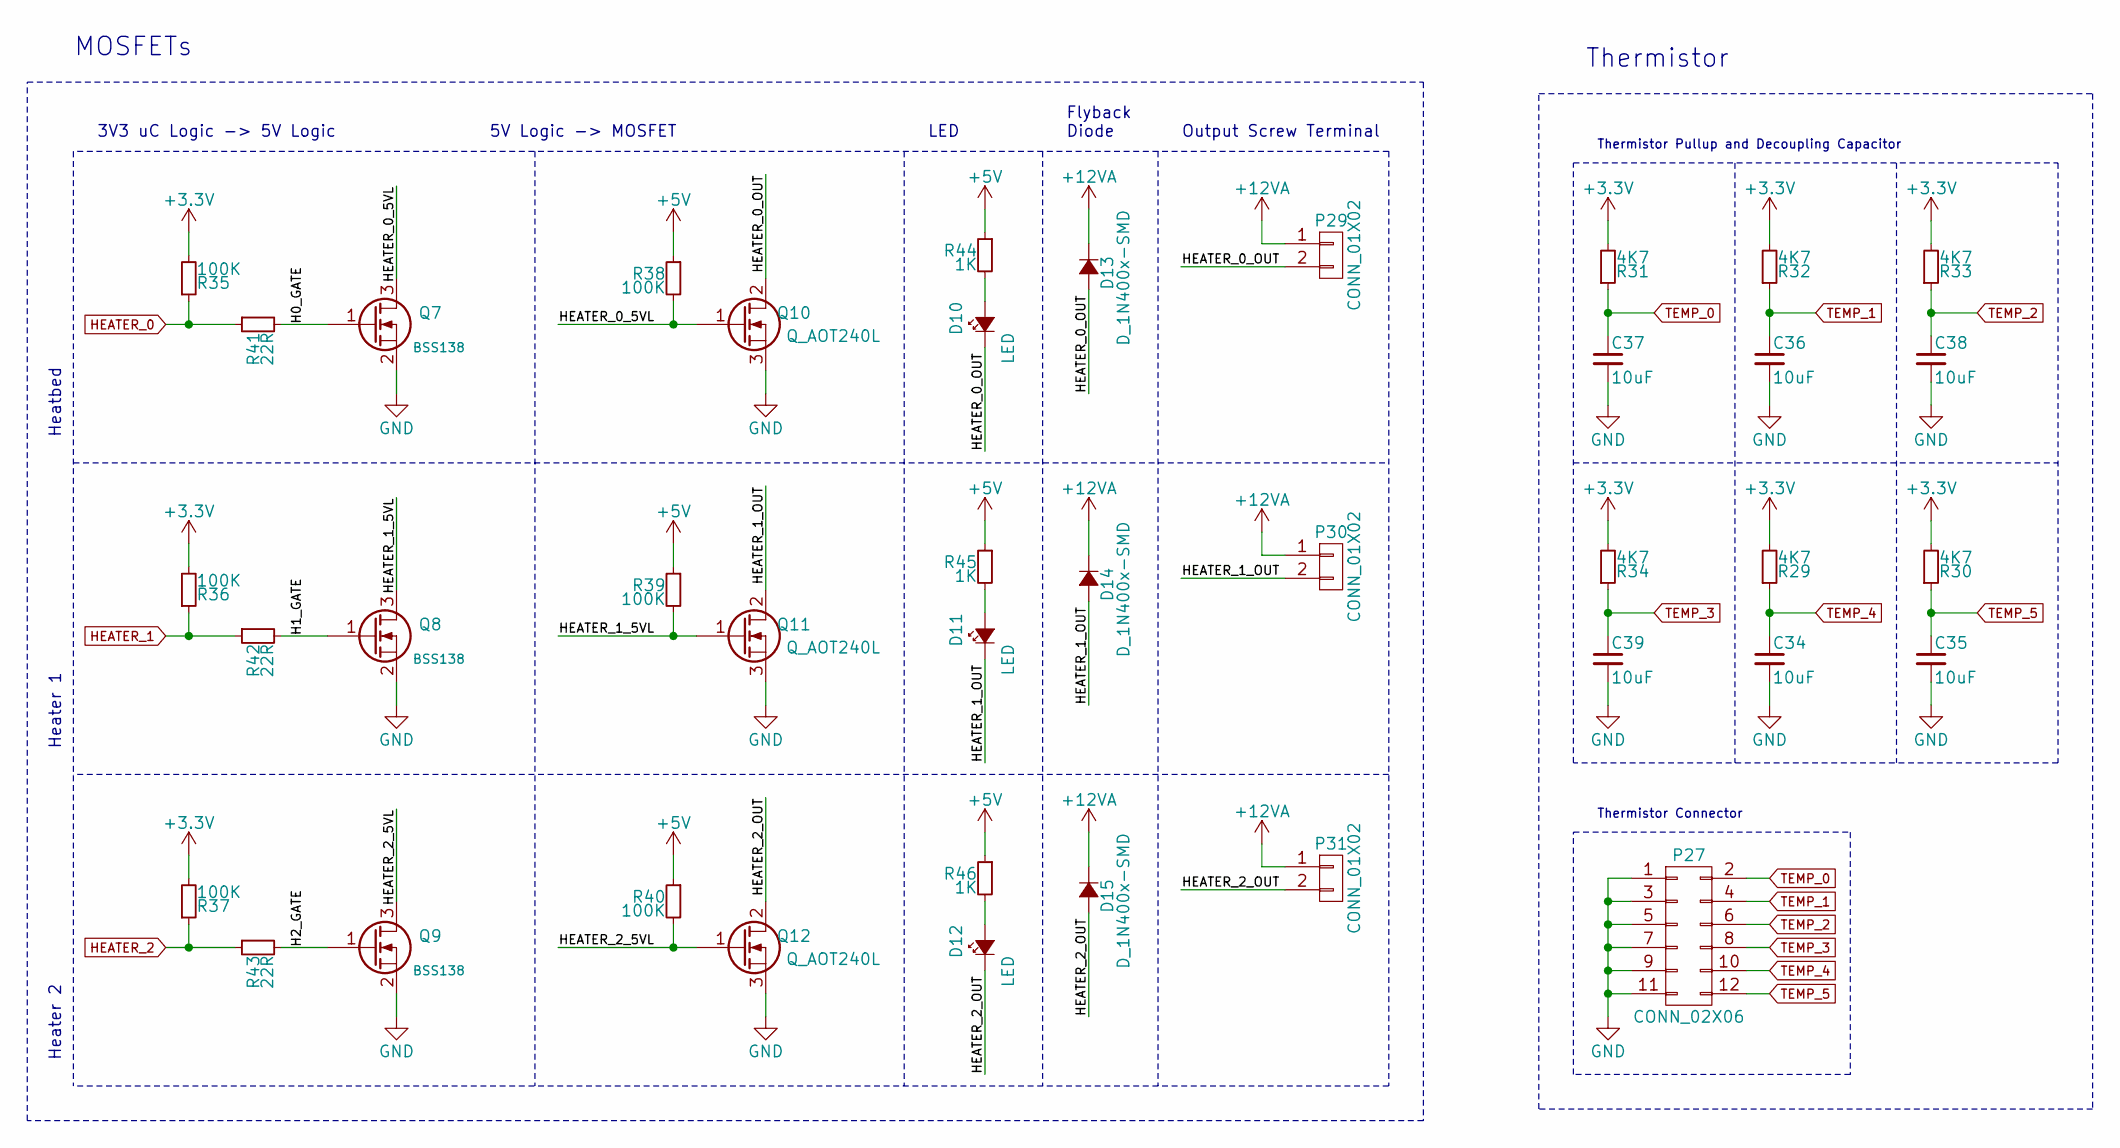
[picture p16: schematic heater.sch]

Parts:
C34, C35, C36, C37, C38, C39: 10uF; C_0805_HandSoldering
D10, D11, D12: LED; LED_0805
D13, D14, D15: D_1N400x-SMD; DO-214AC.SMA
P27: CONN_02X06; Pin_Header_Straight_2x06
P29, P30, P31: CONN_01X02; screw-5-2P
Q7, Q8, Q9: BSS138; SOT-23
Q10, Q11, Q12: Q_AOT240L; TO-220_Neutral123_Vertical_LargePads
R29, R30, R31, R32, R33, R34: 4K7; R_0805_HandSoldering
R35, R36, R37, R38, R39, R40: 100K; R_0805_HandSoldering
R41, R42, R43: 22R; R_0805_HandSoldering
R44, R45, R46: 1K; R_0805_HandSoldering

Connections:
+5V: R38.1, R39.1, R40.1, R44.1, R45.1, R46.1; also elsewhere on the board
+12VA: D13.1 (K), D14.1 (K), D15.1 (K), P29.1, P30.1, P31.1; also elsewhere on the board
/Heater/H0_GATE: Q7.1 (G), R41.2
/Heater/H1_GATE: Q8.1 (G), R42.2
/Heater/H2_GATE: Q9.1 (G), R43.2
/Heater/HEATER_0_5VL: Q7.3 (D), Q10.1 (G), R38.2
/Heater/HEATER_0_OUT: D10.1 (K), D13.2 (A), P29.2, Q10.2 (D)
/Heater/HEATER_1_5VL: Q8.3 (D), Q11.1 (G), R39.2
/Heater/HEATER_1_OUT: D11.1 (K), D14.2 (A), P30.2, Q11.2 (D)
/Heater/HEATER_2_5VL: Q9.3 (D), Q12.1 (G), R40.2
/Heater/HEATER_2_OUT: D12.1 (K), D15.2 (A), P31.2, Q12.2 (D)
GND: C34.2, C35.2, C36.2, C37.2, C38.2, C39.2, P27.1, P27.3, P27.5, P27.7, P27.9, P27.11, Q7.2 (S), Q8.2 (S), Q9.2 (S), Q10.3 (S), Q11.3 (S), Q12.3 (S); also elsewhere on the board
HEATER_0: R35.1, R41.1; also elsewhere on the board
HEATER_1: R36.1, R42.1; also elsewhere on the board
HEATER_2: R37.1, R43.1; also elsewhere on the board
unnamed: D10.2 (A), R44.2
unnamed: D11.2 (A), R45.2
unnamed: D12.2 (A), R46.2
TEMP_0: C37.1, P27.2, R31.1; also elsewhere on the board
TEMP_1: C36.1, P27.4, R32.1; also elsewhere on the board
TEMP_2: C38.1, P27.6, R33.1; also elsewhere on the board
TEMP_3: C39.1, P27.8, R34.1; also elsewhere on the board
TEMP_4: C34.1, P27.10, R29.1; also elsewhere on the board
TEMP_5: C35.1, P27.12, R30.1; also elsewhere on the board

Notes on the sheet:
3V3 uC Logic -> 5V Logic
5V Logic -> MOSFET
LED
Flyback Diode
Output Screw Terminal
Heatbed
Heater 1
Heater 2
MOSFETs
Thermistor Pullup and Decoupling Capacitor
Thermistor Connector
Thermistor

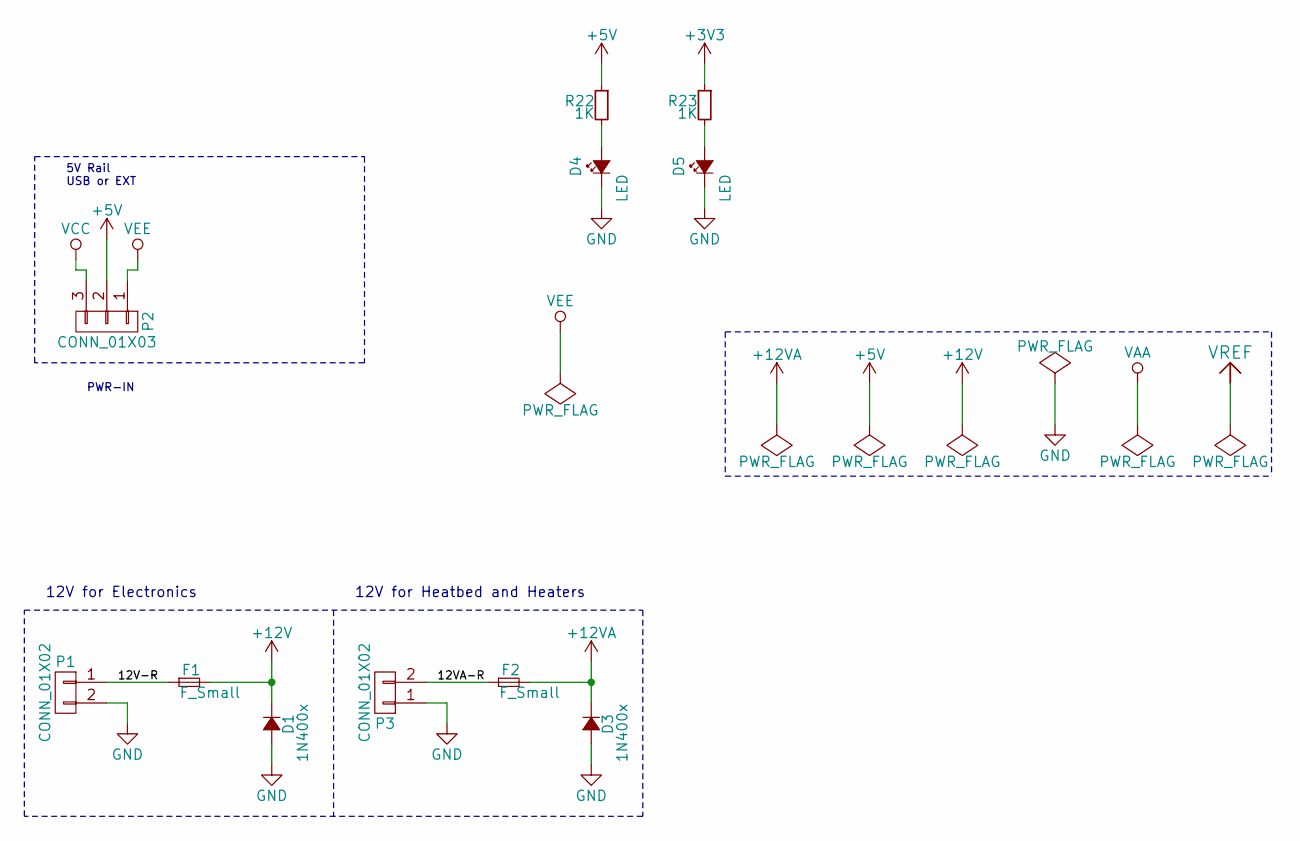
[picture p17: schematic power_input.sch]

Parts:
D1, D3: 1N400x; DO-214AC.SMA
D4, D5: LED; LED_0805
F1, F2: F_Small; MINI-FUSE
P1, P3: CONN_01X02; screw-5-2P
P2: CONN_01X03; bb02-hy03a
R22, R23: 1K; R_0805_HandSoldering

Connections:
+5V: P2.2, R22.1; also elsewhere on the board
+12V: D1.1 (K), F1.2; also elsewhere on the board
+12VA: D3.1 (K), F2.2; also elsewhere on the board
/Power Input/12V-R: F1.1, P1.1
/Power Input/12VA-R: F2.1, P3.2
GND: D1.2 (A), D3.2 (A), D4.1 (K), D5.1 (K), P1.2, P3.1; also elsewhere on the board
unnamed: D4.2 (A), R22.2
unnamed: D5.2 (A), R23.2
VCC: P2.3; also elsewhere on the board
VEE: P2.1; also elsewhere on the board

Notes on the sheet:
PWR-IN
5V Rail USB or EXT
12V for Electronics
12V for Heatbed and Heaters

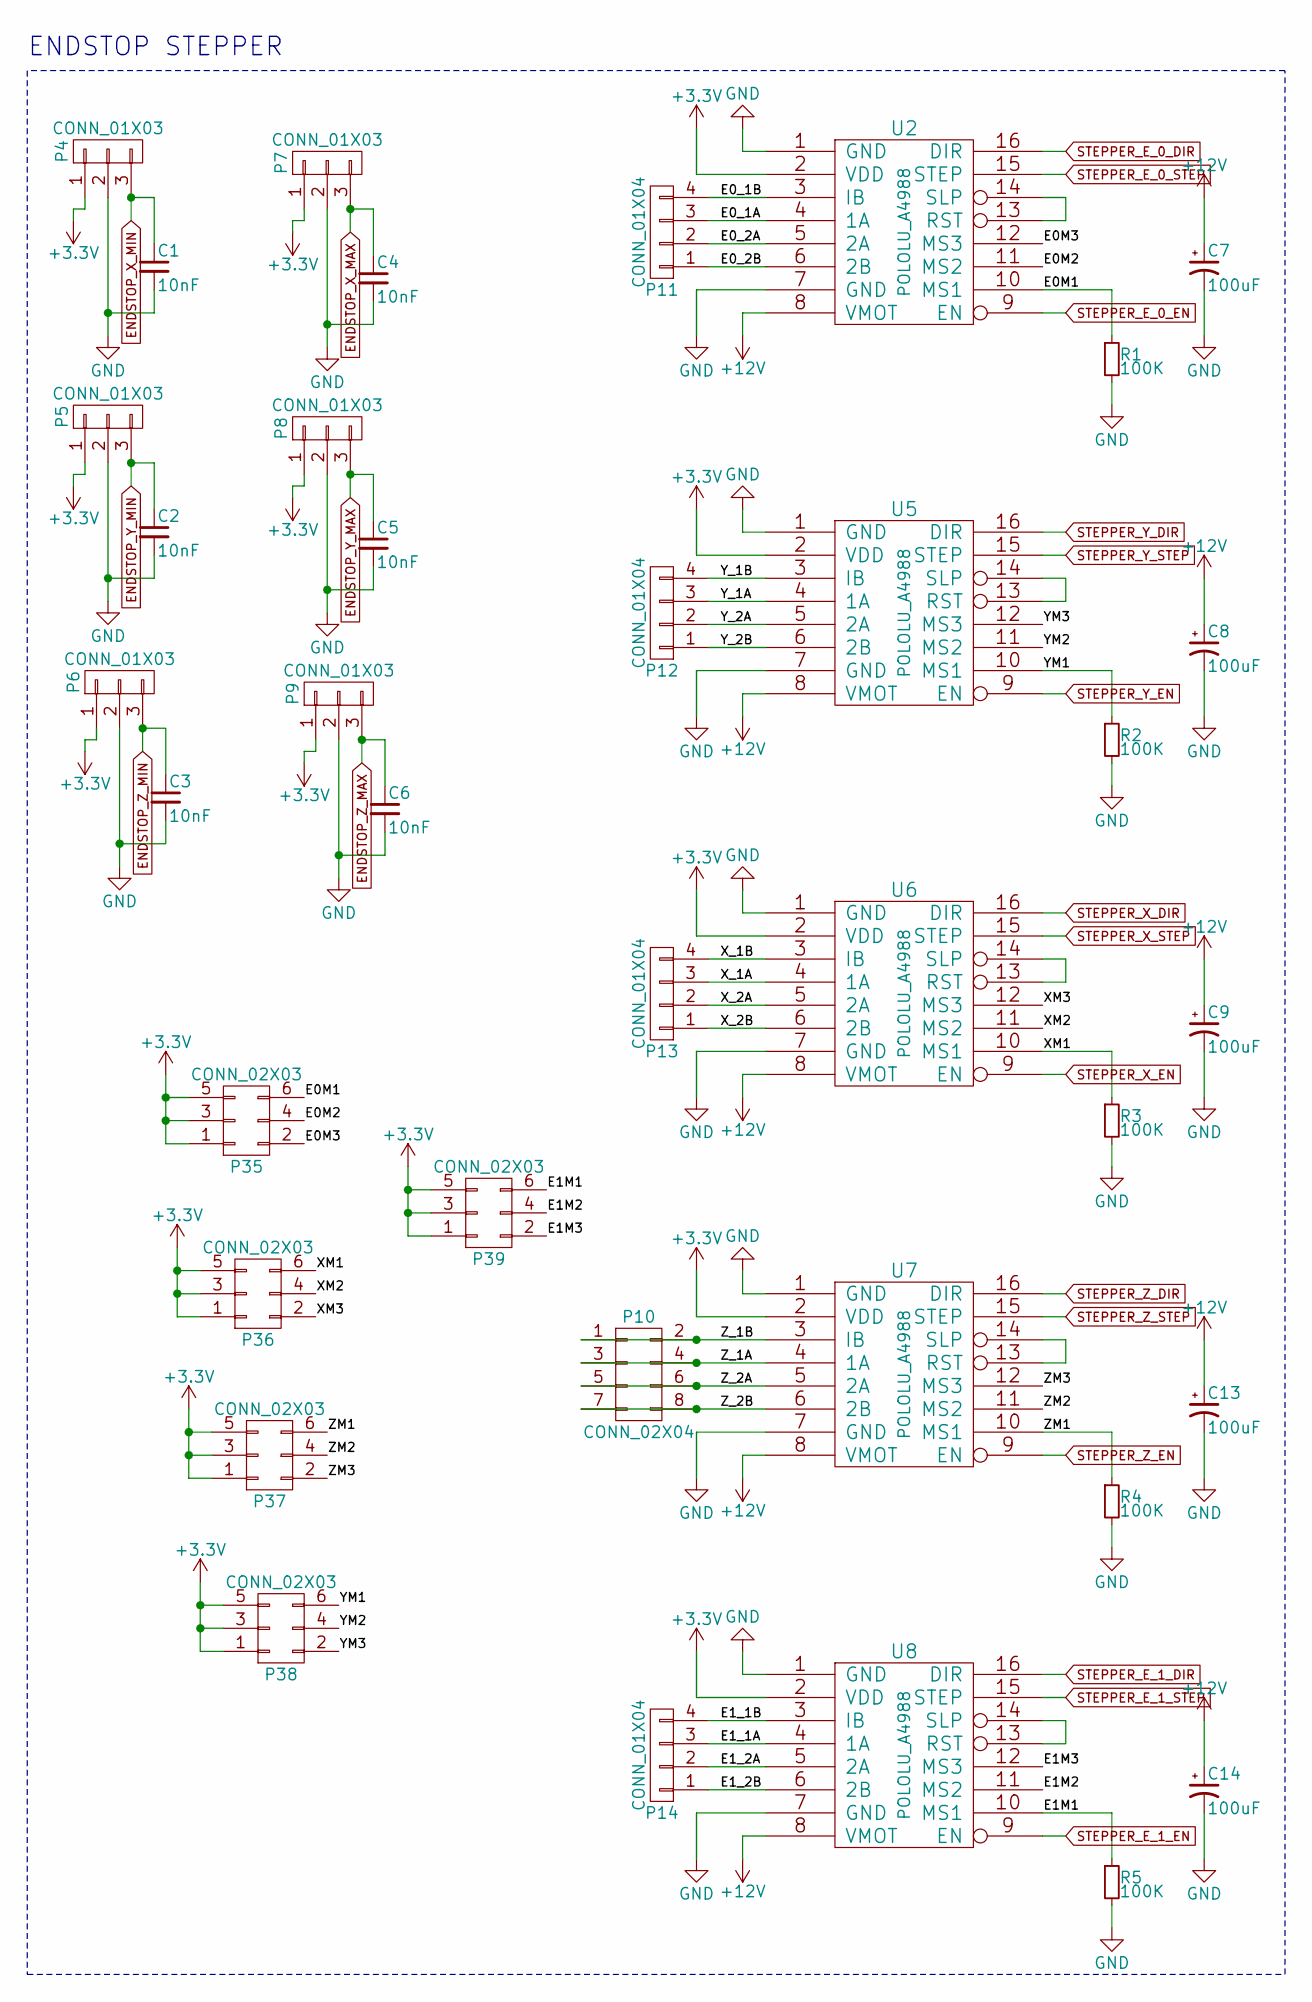
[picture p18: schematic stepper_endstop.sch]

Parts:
C1, C2, C3, C4, C5, C6: 10nF; C_0805_HandSoldering
C7, C8, C9, C13, C14: 100uF; CP-PANASONIC-SMT_D8
P4, P5, P6, P7, P8, P9: CONN_01X03; Pin_Header_Straight_1x03
P10: CONN_02X04; Pin_Header_Straight_2x04
P11, P12, P13, P14: CONN_01X04; Pin_Header_Straight_1x04
P35, P36, P37, P38, P39: CONN_02X03; bb02-hp06
R1, R2, R3, R4, R5: 100K; R_0805_HandSoldering
U2, U5, U6, U7, U8: POLOLU_A4988; SWDIP8_.6W

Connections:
+12V: C7.1, C8.1, C9.1, C13.1, C14.1, U2.8 (VMOT), U5.8 (VMOT), U6.8 (VMOT), U7.8 (VMOT), U8.8 (VMOT); also elsewhere on the board
/Stepper and Endstop/E0M1: P35.6, R1.1, U2.10 (MS1)
/Stepper and Endstop/E0M2: P35.4, U2.11 (MS2)
/Stepper and Endstop/E0M3: P35.2, U2.12 (MS3)
/Stepper and Endstop/E0_1A: P11.3, U2.4 (1A)
/Stepper and Endstop/E0_1B: P11.4, U2.3 (IB)
/Stepper and Endstop/E0_2A: P11.2, U2.5 (2A)
/Stepper and Endstop/E0_2B: P11.1, U2.6 (2B)
/Stepper and Endstop/E1M1: P39.6, R5.1, U8.10 (MS1)
/Stepper and Endstop/E1M2: P39.4, U8.11 (MS2)
/Stepper and Endstop/E1M3: P39.2, U8.12 (MS3)
/Stepper and Endstop/E1_1A: P14.3, U8.4 (1A)
/Stepper and Endstop/E1_1B: P14.4, U8.3 (IB)
/Stepper and Endstop/E1_2A: P14.2, U8.5 (2A)
/Stepper and Endstop/E1_2B: P14.1, U8.6 (2B)
/Stepper and Endstop/XM1: P36.6, R3.1, U6.10 (MS1)
/Stepper and Endstop/XM2: P36.4, U6.11 (MS2)
/Stepper and Endstop/XM3: P36.2, U6.12 (MS3)
/Stepper and Endstop/X_1A: P13.3, U6.4 (1A)
/Stepper and Endstop/X_1B: P13.4, U6.3 (IB)
/Stepper and Endstop/X_2A: P13.2, U6.5 (2A)
/Stepper and Endstop/X_2B: P13.1, U6.6 (2B)
/Stepper and Endstop/YM1: P38.6, R2.1, U5.10 (MS1)
/Stepper and Endstop/YM2: P38.4, U5.11 (MS2)
/Stepper and Endstop/YM3: P38.2, U5.12 (MS3)
/Stepper and Endstop/Y_1A: P12.3, U5.4 (1A)
/Stepper and Endstop/Y_1B: P12.4, U5.3 (IB)
/Stepper and Endstop/Y_2A: P12.2, U5.5 (2A)
/Stepper and Endstop/Y_2B: P12.1, U5.6 (2B)
/Stepper and Endstop/ZM1: P37.6, R4.1, U7.10 (MS1)
/Stepper and Endstop/ZM2: P37.4, U7.11 (MS2)
/Stepper and Endstop/ZM3: P37.2, U7.12 (MS3)
/Stepper and Endstop/Z_1A: P10.3, P10.4, U7.4 (1A)
/Stepper and Endstop/Z_1B: P10.1, P10.2, U7.3 (IB)
/Stepper and Endstop/Z_2A: P10.5, P10.6, U7.5 (2A)
/Stepper and Endstop/Z_2B: P10.7, P10.8, U7.6 (2B)
ENDSTOP_X_MAX: C4.1, P7.3; also elsewhere on the board
ENDSTOP_X_MIN: C1.1, P4.3; also elsewhere on the board
ENDSTOP_Y_MAX: C5.1, P8.3; also elsewhere on the board
ENDSTOP_Y_MIN: C2.1, P5.3; also elsewhere on the board
ENDSTOP_Z_MAX: C6.1, P9.3; also elsewhere on the board
ENDSTOP_Z_MIN: C3.1, P6.3; also elsewhere on the board
GND: C1.2, C2.2, C3.2, C4.2, C5.2, C6.2, C7.2, C8.2, C9.2, C13.2, C14.2, P4.2, P5.2, P6.2, P7.2, P8.2, P9.2, R1.2, R2.2, R3.2, R4.2, R5.2, U2.1 (GND), U2.7 (GND), U5.1 (GND), U5.7 (GND), U6.1 (GND), U6.7 (GND), U7.1 (GND), U7.7 (GND), U8.1 (GND), U8.7 (GND); also elsewhere on the board
unnamed: U2.13 (RST), U2.14 (SLP)
unnamed: U5.13 (RST), U5.14 (SLP)
unnamed: U6.13 (RST), U6.14 (SLP)
unnamed: U7.13 (RST), U7.14 (SLP)
unnamed: U8.13 (RST), U8.14 (SLP)
STEPPER_E_0_DIR: U2.16 (DIR); also elsewhere on the board
STEPPER_E_0_EN: U2.9 (EN); also elsewhere on the board
STEPPER_E_0_STEP: U2.15 (STEP); also elsewhere on the board
STEPPER_E_1_DIR: U8.16 (DIR); also elsewhere on the board
STEPPER_E_1_EN: U8.9 (EN); also elsewhere on the board
STEPPER_E_1_STEP: U8.15 (STEP); also elsewhere on the board
STEPPER_X_DIR: U6.16 (DIR); also elsewhere on the board
STEPPER_X_EN: U6.9 (EN); also elsewhere on the board
STEPPER_X_STEP: U6.15 (STEP); also elsewhere on the board
STEPPER_Y_DIR: U5.16 (DIR); also elsewhere on the board
STEPPER_Y_EN: U5.9 (EN); also elsewhere on the board
STEPPER_Y_STEP: U5.15 (STEP); also elsewhere on the board
STEPPER_Z_DIR: U7.16 (DIR); also elsewhere on the board
STEPPER_Z_EN: U7.9 (EN); also elsewhere on the board
STEPPER_Z_STEP: U7.15 (STEP); also elsewhere on the board

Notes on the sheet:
ENDSTOP STEPPER

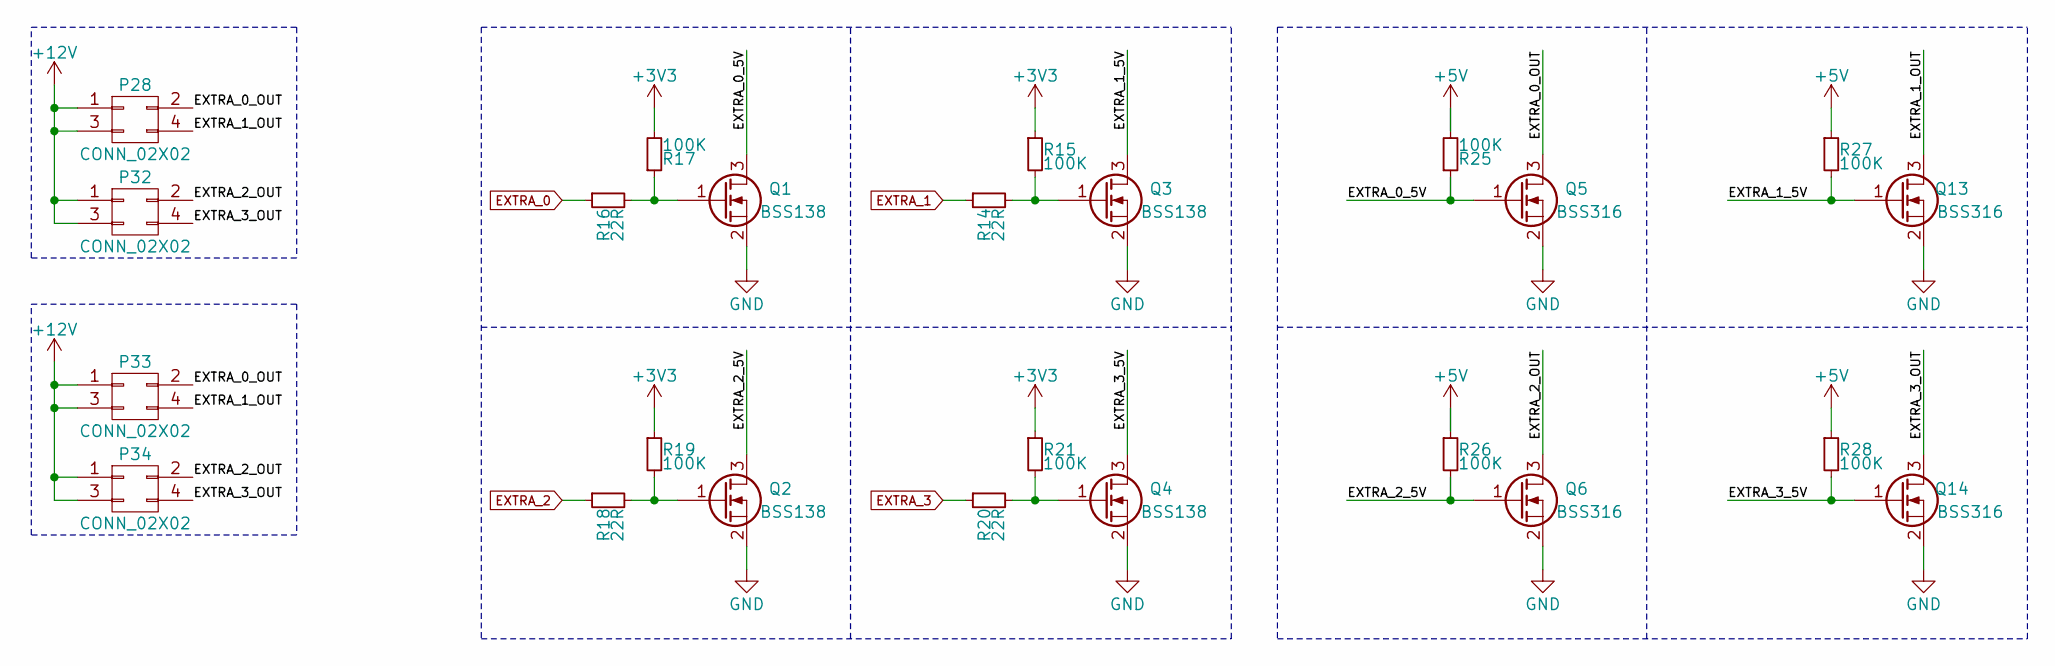
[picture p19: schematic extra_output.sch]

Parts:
P28, P32: CONN_02X02; pt_1,5-4-3,5-h
P33, P34: CONN_02X02; Pin_Header_Straight_1x04
Q1, Q2, Q3, Q4: BSS138; SOT-23
Q5, Q6, Q13, Q14: BSS316; SOT-23
R14, R16, R18, R20: 22R; R_0805
R15, R17, R19, R21, R25, R26, R27, R28: 100K; R_0805

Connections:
+5V: R25.2, R26.1, R27.1, R28.1; also elsewhere on the board
+12V: P28.1, P28.3, P32.1, P32.3, P33.1, P33.3, P34.1, P34.3; also elsewhere on the board
/Extra Power Output/EXTRA_0_5V: Q1.3 (D), Q5.1 (G), R25.1
/Extra Power Output/EXTRA_0_OUT: P28.2, P33.2, Q5.3 (D)
/Extra Power Output/EXTRA_1_5V: Q3.3 (D), Q13.1 (G), R27.2
/Extra Power Output/EXTRA_1_OUT: P28.4, P33.4, Q13.3 (D)
/Extra Power Output/EXTRA_2_5V: Q2.3 (D), Q6.1 (G), R26.2
/Extra Power Output/EXTRA_2_OUT: P32.2, P34.2, Q6.3 (D)
/Extra Power Output/EXTRA_3_5V: Q4.3 (D), Q14.1 (G), R28.2
/Extra Power Output/EXTRA_3_OUT: P32.4, P34.4, Q14.3 (D)
EXTRA_0: R16.1; also elsewhere on the board
EXTRA_1: R14.1; also elsewhere on the board
EXTRA_2: R18.1; also elsewhere on the board
EXTRA_3: R20.1; also elsewhere on the board
GND: Q1.2 (S), Q2.2 (S), Q3.2 (S), Q4.2 (S), Q5.2 (S), Q6.2 (S), Q13.2 (S), Q14.2 (S); also elsewhere on the board
unnamed: Q1.1 (G), R16.2, R17.1
unnamed: Q2.1 (G), R18.2, R19.2
unnamed: Q3.1 (G), R14.2, R15.2
unnamed: Q4.1 (G), R20.2, R21.2

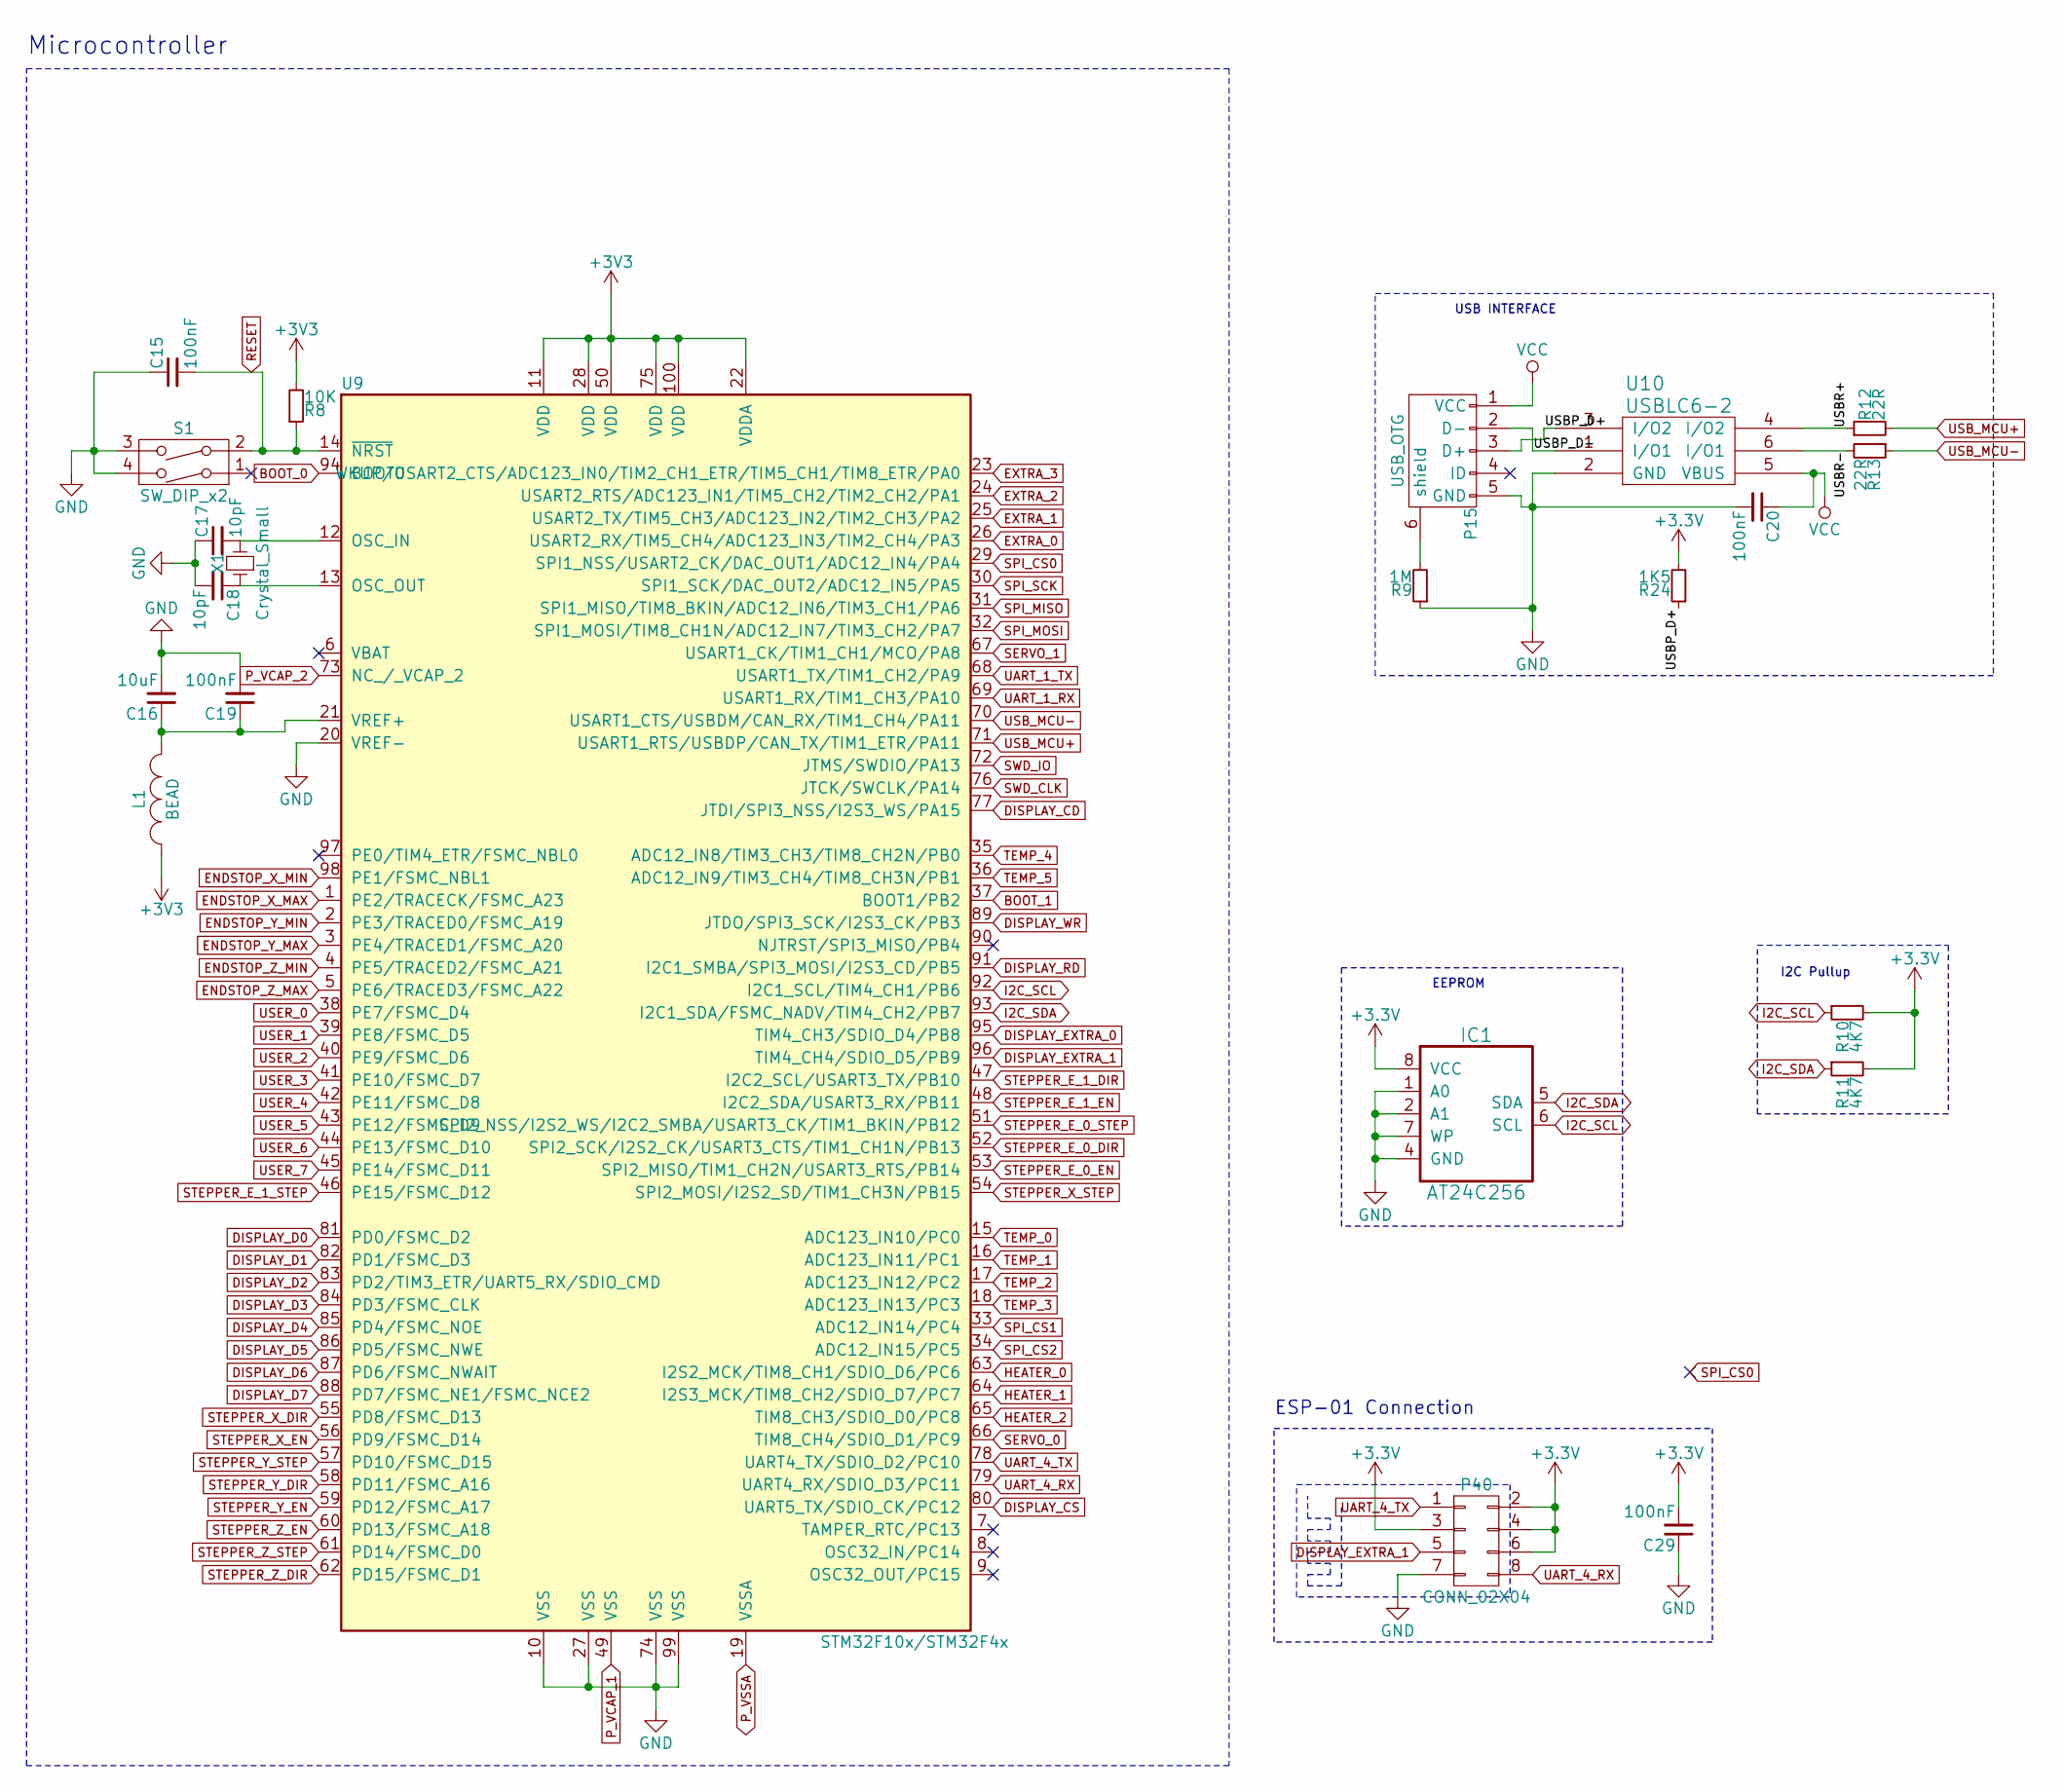
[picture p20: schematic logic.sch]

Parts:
C15: 100nF; R_0805_HandSoldering
C16: 10uF; C_0805_HandSoldering
C17, C18: 10pF; R_0805_HandSoldering
C19, C20, C29: 100nF; C_0805_HandSoldering
IC1: AT24C256; SOIC-8_3.9x4.9mm_Pitch1.27mm
L1: BEAD; C_0805_HandSoldering
P15: USB_OTG; USB_Mini-B
P40: CONN_02X04; Pin_Header_Straight_2x04
R8: 10K; R_0805_HandSoldering
R9: 1M; R_0805_HandSoldering
R10, R11: 4K7; R_0805_HandSoldering
R12, R13: 22R; R_0805_HandSoldering
R24: 1K5; R_0805_HandSoldering
S1: SW_DIP_x2; SMD-BUTTON-6MM
U9: STM32F10x/STM32F4x; LQFP100-14x14
U10: USBLC6-2; SOT32-6L
X1: Crystal_Small; 2P-5032

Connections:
/Logic/USBP_D+: P15.3 (D+), R24.1, U10.3 (I/O2)
/Logic/USBP_D-: P15.2 (D-), U10.1 (I/O1)
/Logic/USBR+: R12.1, U10.4 (I/O2)
/Logic/USBR-: R13.2, U10.6 (I/O1)
BOOT_0: U9.94 (BOOT0); also elsewhere on the board
BOOT_1: U9.37 (BOOT1/PB2); also elsewhere on the board
DISPLAY_CD: U9.77 (JTDI/SPI3_NSS/I2S3_WS/PA15); also elsewhere on the board
DISPLAY_CS: U9.80 (UART5_TX/SDIO_CK/PC12); also elsewhere on the board
DISPLAY_D0: U9.81 (PD0/FSMC_D2); also elsewhere on the board
DISPLAY_D1: U9.82 (PD1/FSMC_D3); also elsewhere on the board
DISPLAY_D2: U9.83 (PD2/TIM3_ETR/UART5_RX/SDIO_CMD); also elsewhere on the board
DISPLAY_D3: U9.84 (PD3/FSMC_CLK); also elsewhere on the board
DISPLAY_D4: U9.85 (PD4/FSMC_NOE); also elsewhere on the board
DISPLAY_D5: U9.86 (PD5/FSMC_NWE); also elsewhere on the board
DISPLAY_D6: U9.87 (PD6/FSMC_NWAIT); also elsewhere on the board
DISPLAY_D7: U9.88 (PD7/FSMC_NE1/FSMC_NCE2); also elsewhere on the board
DISPLAY_EXTRA_0: U9.95 (TIM4_CH3/SDIO_D4/PB8); also elsewhere on the board
DISPLAY_EXTRA_1: P40.5, U9.96 (TIM4_CH4/SDIO_D5/PB9)
DISPLAY_RD: U9.91 (I2C1_SMBA/SPI3_MOSI/I2S3_CD/PB5); also elsewhere on the board
DISPLAY_WR: U9.89 (JTDO/SPI3_SCK/I2S3_CK/PB3); also elsewhere on the board
ENDSTOP_X_MAX: U9.1 (PE2/TRACECK/FSMC_A23); also elsewhere on the board
ENDSTOP_X_MIN: U9.98 (PE1/FSMC_NBL1); also elsewhere on the board
ENDSTOP_Y_MAX: U9.3 (PE4/TRACED1/FSMC_A20); also elsewhere on the board
ENDSTOP_Y_MIN: U9.2 (PE3/TRACED0/FSMC_A19); also elsewhere on the board
ENDSTOP_Z_MAX: U9.5 (PE6/TRACED3/FSMC_A22); also elsewhere on the board
ENDSTOP_Z_MIN: U9.4 (PE5/TRACED2/FSMC_A21); also elsewhere on the board
EXTRA_0: U9.26 (USART2_RX/TIM5_CH4/ADC123_IN3/TIM2_CH4/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); also elsewhere on the board
EXTRA_1: U9.25 (USART2_TX/TIM5_CH3/ADC123_IN2/TIM2_CH3/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); also elsewhere on the board
EXTRA_2: U9.24 (USART2_RTS/ADC123_IN1/TIM5_CH2/TIM2_CH2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); also elsewhere on the board
EXTRA_3: U9.23 (WKUP/USART2_CTS/ADC123_IN0/TIM2_CH1_ETR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); also elsewhere on the board
GND: C15.1, C16.2, C17.1, C18.2, C19.2, C20.2, C29.1, IC1.1 (A0), IC1.2 (A1), IC1.4 (GND), IC1.7 (WP), P15.5 (GND), P40.7, R9.1, S1.3, S1.4, U9.10 (VSS), U9.20 (VREF-), U9.27 (VSS), U9.74 (VSS), U9.99 (VSS), U10.2 (GND); also elsewhere on the board
HEATER_0: U9.63 (I2S2_MCK/TIM8_CH1/SDIO_D6/PC6); also elsewhere on the board
HEATER_1: U9.64 (I2S3_MCK/TIM8_CH2/SDIO_D7/PC7); also elsewhere on the board
HEATER_2: U9.65 (TIM8_CH3/SDIO_D0/PC8); also elsewhere on the board
I2C_SCL: IC1.6 (SCL), R10.1, U9.92 (I2C1_SCL/TIM4_CH1/PB6); also elsewhere on the board
I2C_SDA: IC1.5 (SDA), R11.1, U9.93 (I2C1_SDA/FSMC_NADV/TIM4_CH2/PB7); also elsewhere on the board
unnamed: C16.1, C19.1, L1.2, U9.21 (VREF+)
unnamed: C17.2, U9.12 (OSC_IN), X1.2
unnamed: C18.1, U9.13 (OSC_OUT), X1.1
unnamed: P15.6 (shield), R9.2
P_VCAP_1: U9.49 (VSS); also elsewhere on the board
P_VCAP_2: U9.73 (NC_/_VCAP_2); also elsewhere on the board
P_VSSA: U9.19 (VSSA); also elsewhere on the board
RESET: C15.2, R8.1, S1.2, U9.14 (~NRST); also elsewhere on the board
SERVO_0: U9.66 (TIM8_CH4/SDIO_D1/PC9); also elsewhere on the board
SERVO_1: U9.67 (USART1_CK/TIM1_CH1/MCO/PA8); also elsewhere on the board
SPI_CS0: U9.29 (SPI1_NSS/USART2_CK/DAC_OUT1/ADC12_IN4/P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)
SPI_CS1: U9.33 (ADC12_IN14/PC4); also elsewhere on the board
SPI_CS2: U9.34 (ADC12_IN15/PC5); also elsewhere on the board
SPI_MISO: U9.31 (SPI1_MISO/TIM8_BKIN/ADC12_IN6/TIM3_CH1/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); also elsewhere on the board
SPI_MOSI: U9.32 (SPI1_MOSI/TIM8_CH1N/ADC12_IN7/TIM3_CH2/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); also elsewhere on the board
SPI_SCK: U9.30 (SPI1_SCK/DAC_OUT2/ADC12_IN5/PA5); also elsewhere on the board
STEPPER_E_0_DIR: U9.52 (SPI2_SCK/I2S2_CK/USART3_CTS/TIM1_CH1N/P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); also elsewhere on the board
STEPPER_E_0_EN: U9.53 (SPI2_MISO/TIM1_CH2N/USART3_RTS/PB14); also elsewhere on the board
STEPPER_E_0_STEP: U9.51 (SPI2_NSS/I2S2_WS/I2C2_SMBA/USART3_CK/TI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); also elsewhere on the board
STEPPER_E_1_DIR: U9.47 (I2C2_SCL/USART3_TX/PB10); also elsewhere on the board
STEPPER_E_1_EN: U9.48 (I2C2_SDA/USART3_RX/PB11); also elsewhere on the board
STEPPER_E_1_STEP: U9.46 (PE15/FSMC_D12); also elsewhere on the board
STEPPER_X_DIR: U9.55 (PD8/FSMC_D13); also elsewhere on the board
STEPPER_X_EN: U9.56 (PD9/FSMC_D14); also elsewhere on the board
STEPPER_X_STEP: U9.54 (SPI2_MOSI/I2S2_SD/TIM1_CH3N/PB15); also elsewhere on the board
STEPPER_Y_DIR: U9.58 (PD11/FSMC_A16); also elsewhere on the board
STEPPER_Y_EN: U9.59 (PD12/FSMC_A17); also elsewhere on the board
STEPPER_Y_STEP: U9.57 (PD10/FSMC_D15); also elsewhere on the board
STEPPER_Z_DIR: U9.62 (PD15/FSMC_D1); also elsewhere on the board
STEPPER_Z_EN: U9.60 (PD13/FSMC_A18); also elsewhere on the board
STEPPER_Z_STEP: U9.61 (PD14/FSMC_D0); also elsewhere on the board
SWD_CLK: U9.76 (JTCK/SWCLK/PA14); also elsewhere on the board
SWD_IO: U9.72 (JTMS/SWDIO/PA13); also elsewhere on the board
TEMP_0: U9.15 (ADC123_IN10/PC0); also elsewhere on the board
TEMP_1: U9.16 (ADC123_IN11/PC1); also elsewhere on the board
TEMP_2: U9.17 (ADC123_IN12/PC2); also elsewhere on the board
TEMP_3: U9.18 (ADC123_IN13/PC3); also elsewhere on the board
TEMP_4: U9.35 (ADC12_IN8/TIM3_CH3/TIM8_CH2N/PB0); also elsewhere on the board
TEMP_5: U9.36 (ADC12_IN9/TIM3_CH4/TIM8_CH3N/PB1); also elsewhere on the board
UART_1_RX: U9.69 (USART1_RX/TIM1_CH3/PA10); also elsewhere on the board
UART_1_TX: U9.68 (USART1_TX/TIM1_CH2/PA9); also elsewhere on the board
UART_4_RX: P40.8, U9.79 (UART4_RX/SDIO_D3/PC11)
UART_4_TX: P40.1, U9.78 (UART4_TX/SDIO_D2/PC10)
USB_MCU+: R12.2, U9.71 (USART1_RTS/USBDP/CAN_TX/TIM1_ETR/PA11)
USB_MCU-: R13.1, U9.70 (USART1_CTS/USBDM/CAN_RX/TIM1_CH4/PA11)
USER_0: U9.38 (PE7/FSMC_D4); also elsewhere on the board
USER_1: U9.39 (PE8/FSMC_D5); also elsewhere on the board
USER_2: U9.40 (PE9/FSMC_D6); also elsewhere on the board
USER_3: U9.41 (PE10/FSMC_D7); also elsewhere on the board
USER_4: U9.42 (PE11/FSMC_D8); also elsewhere on the board
USER_5: U9.43 (PE12/FSMC_D9); also elsewhere on the board
USER_6: U9.44 (PE13/FSMC_D10); also elsewhere on the board
USER_7: U9.45 (PE14/FSMC_D11); also elsewhere on the board
VCC: C20.1, P15.1 (VCC), U10.5 (VBUS); also elsewhere on the board

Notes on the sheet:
EEPROM
I2C Pullup
Microcontroller
USB INTERFACE
ESP-01 Connection

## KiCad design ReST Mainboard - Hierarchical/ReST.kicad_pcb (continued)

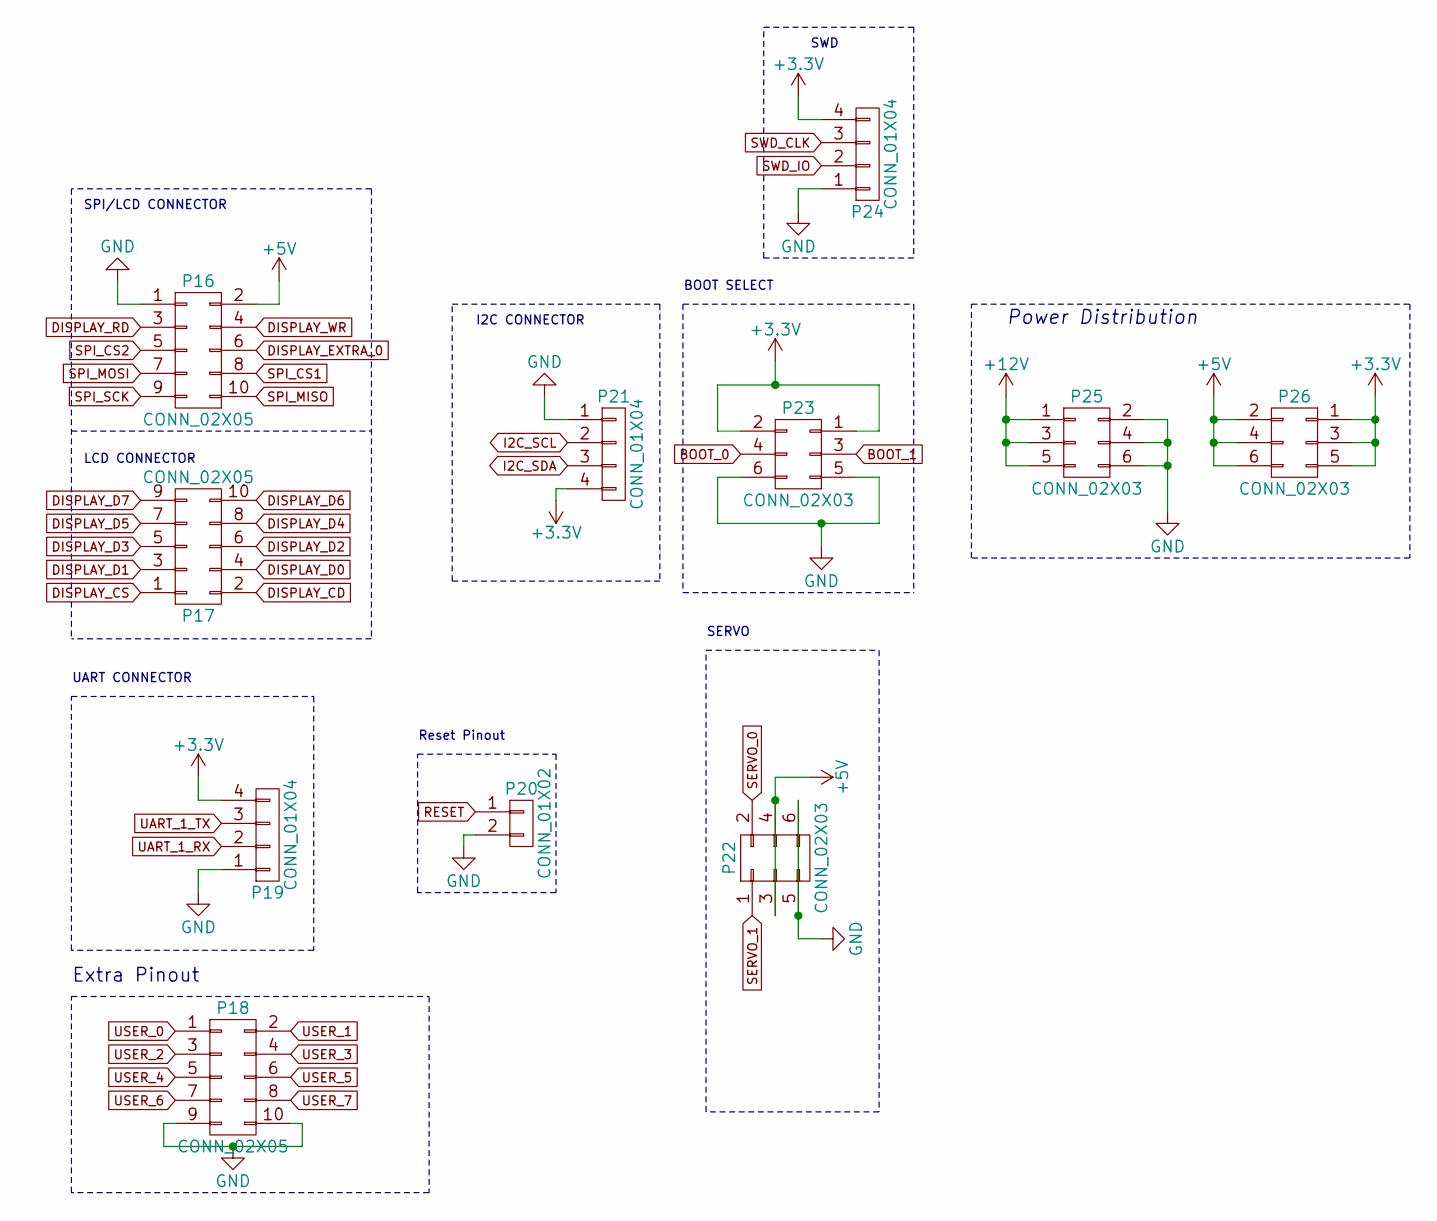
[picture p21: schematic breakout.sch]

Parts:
P16, P17: CONN_02X05; IDC_Header_Straight_10pins
P18: CONN_02X05; Pin_Header_Straight_2x05
P19, P24: CONN_01X04; bb02-hy04a
P20: CONN_01X02; Pin_Header_Straight_1x02
P21: CONN_01X04; Pin_Header_Straight_1x04
P22, P23: CONN_02X03; bb02-hp06
P25, P26: CONN_02X03; Pin_Header_Straight_2x03

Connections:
+5V: P16.2, P22.3, P22.4, P26.2, P26.4, P26.6; also elsewhere on the board
+12V: P25.1, P25.3, P25.5; also elsewhere on the board
BOOT_0: P23.4; also elsewhere on the board
BOOT_1: P23.3; also elsewhere on the board
DISPLAY_CD: P17.2; also elsewhere on the board
DISPLAY_CS: P17.1; also elsewhere on the board
DISPLAY_D0: P17.4; also elsewhere on the board
DISPLAY_D1: P17.3; also elsewhere on the board
DISPLAY_D2: P17.6; also elsewhere on the board
DISPLAY_D3: P17.5; also elsewhere on the board
DISPLAY_D4: P17.8; also elsewhere on the board
DISPLAY_D5: P17.7; also elsewhere on the board
DISPLAY_D6: P17.10; also elsewhere on the board
DISPLAY_D7: P17.9; also elsewhere on the board
DISPLAY_EXTRA_0: P16.6; also elsewhere on the board
DISPLAY_RD: P16.3; also elsewhere on the board
DISPLAY_WR: P16.4; also elsewhere on the board
GND: P16.1, P18.9, P18.10, P19.1, P20.2, P21.1, P22.5, P22.6, P23.5, P23.6, P24.1, P25.2, P25.4, P25.6; also elsewhere on the board
I2C_SCL: P21.2; also elsewhere on the board
I2C_SDA: P21.3; also elsewhere on the board
RESET: P20.1; also elsewhere on the board
SERVO_0: P22.2; also elsewhere on the board
SERVO_1: P22.1; also elsewhere on the board
SPI_CS1: P16.8; also elsewhere on the board
SPI_CS2: P16.5; also elsewhere on the board
SPI_MISO: P16.10; also elsewhere on the board
SPI_MOSI: P16.7; also elsewhere on the board
SPI_SCK: P16.9; also elsewhere on the board
SWD_CLK: P24.3; also elsewhere on the board
SWD_IO: P24.2; also elsewhere on the board
UART_1_RX: P19.2; also elsewhere on the board
UART_1_TX: P19.3; also elsewhere on the board
USER_0: P18.1; also elsewhere on the board
USER_1: P18.2; also elsewhere on the board
USER_2: P18.3; also elsewhere on the board
USER_3: P18.4; also elsewhere on the board
USER_4: P18.5; also elsewhere on the board
USER_5: P18.6; also elsewhere on the board
USER_6: P18.7; also elsewhere on the board
USER_7: P18.8; also elsewhere on the board

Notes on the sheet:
Power Distribution
SPI/LCD CONNECTOR
BOOT SELECT
I2C CONNECTOR
SERVO
UART CONNECTOR
SWD
LCD CONNECTOR
Extra Pinout
Reset Pinout

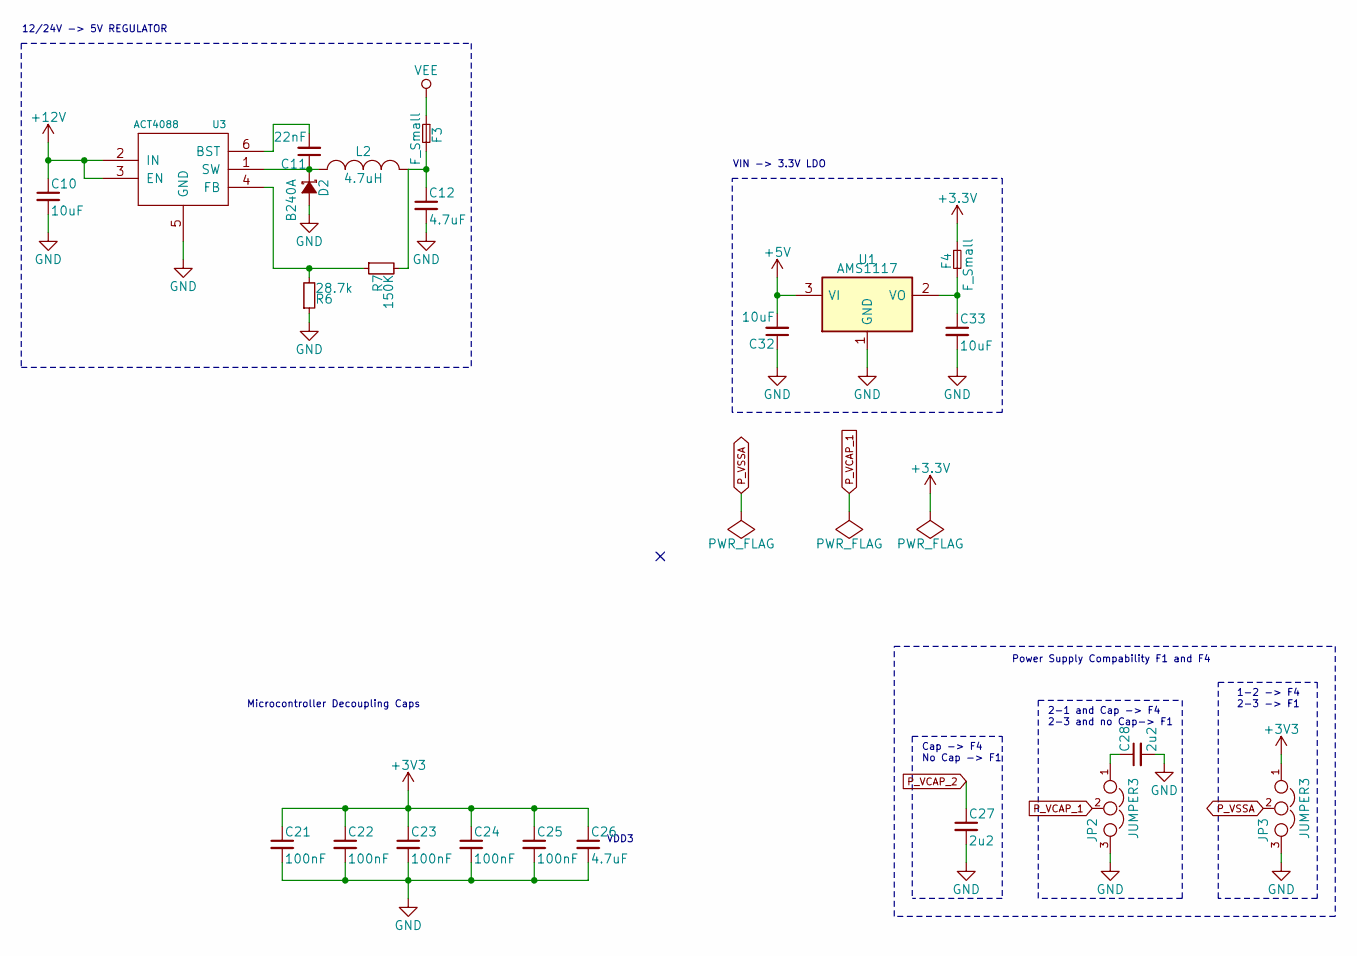
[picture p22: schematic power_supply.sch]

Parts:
C10: 10uF; C_1206_HandSoldering
C11: 22nF; C_0805_HandSoldering
C12, C26: 4.7uF; C_0805_HandSoldering
C21, C22, C23, C24, C25: 100nF; C_0805_HandSoldering
C27, C28: 2u2; C_0805_HandSoldering
C32, C33: 10uF; C_0805_HandSoldering
D2: B240A; DO-214AC.SMA
F3: F_Small; FUSE-1812
F4: F_Small; R_0805_HandSoldering
JP2, JP3: JUMPER3; S_JUMPER_3
L2: 4.7uH; CD32
R6: 28.7k; R_0805_HandSoldering
R7: 150K; R_0805_HandSoldering
U1: AMS1117; SOT-223
U3: ACT4088; SOT-23-6

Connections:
+5V: C32.2, U1.3 (VI); also elsewhere on the board
+12V: C10.1, U3.2 (IN), U3.3 (EN); also elsewhere on the board
GND: C10.2, C12.2, C21.2, C22.2, C23.2, C24.2, C25.2, C26.2, C27.2, C28.2, C32.1, C33.2, D2.2 (A), JP2.3, JP3.3, R6.1, U1.1 (GND), U3.5 (GND); also elsewhere on the board
unnamed: C11.1, D2.1 (K), L2.1, U3.1 (SW)
unnamed: C11.2, U3.6 (BST)
unnamed: C12.1, F3.2, L2.2, R7.2
unnamed: C28.1, JP2.1
unnamed: C33.1, F4.2, U1.2 (VO)
unnamed: R6.2, R7.1, U3.4 (FB)
P_VCAP_1: JP2.2; also elsewhere on the board
P_VCAP_2: C27.1; also elsewhere on the board
P_VSSA: JP3.2; also elsewhere on the board
VEE: F3.1; also elsewhere on the board

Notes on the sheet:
VIN -> 3.3V LDO
12/24V -> 5V REGULATOR
2-1 and Cap -> F4 2-3 and no Cap-> F1
Cap -> F4 No Cap -> F1
1-2 -> F4 2-3 -> F1
Power Supply Compability F1 and F4
VDD3
Microcontroller Decoupling Caps

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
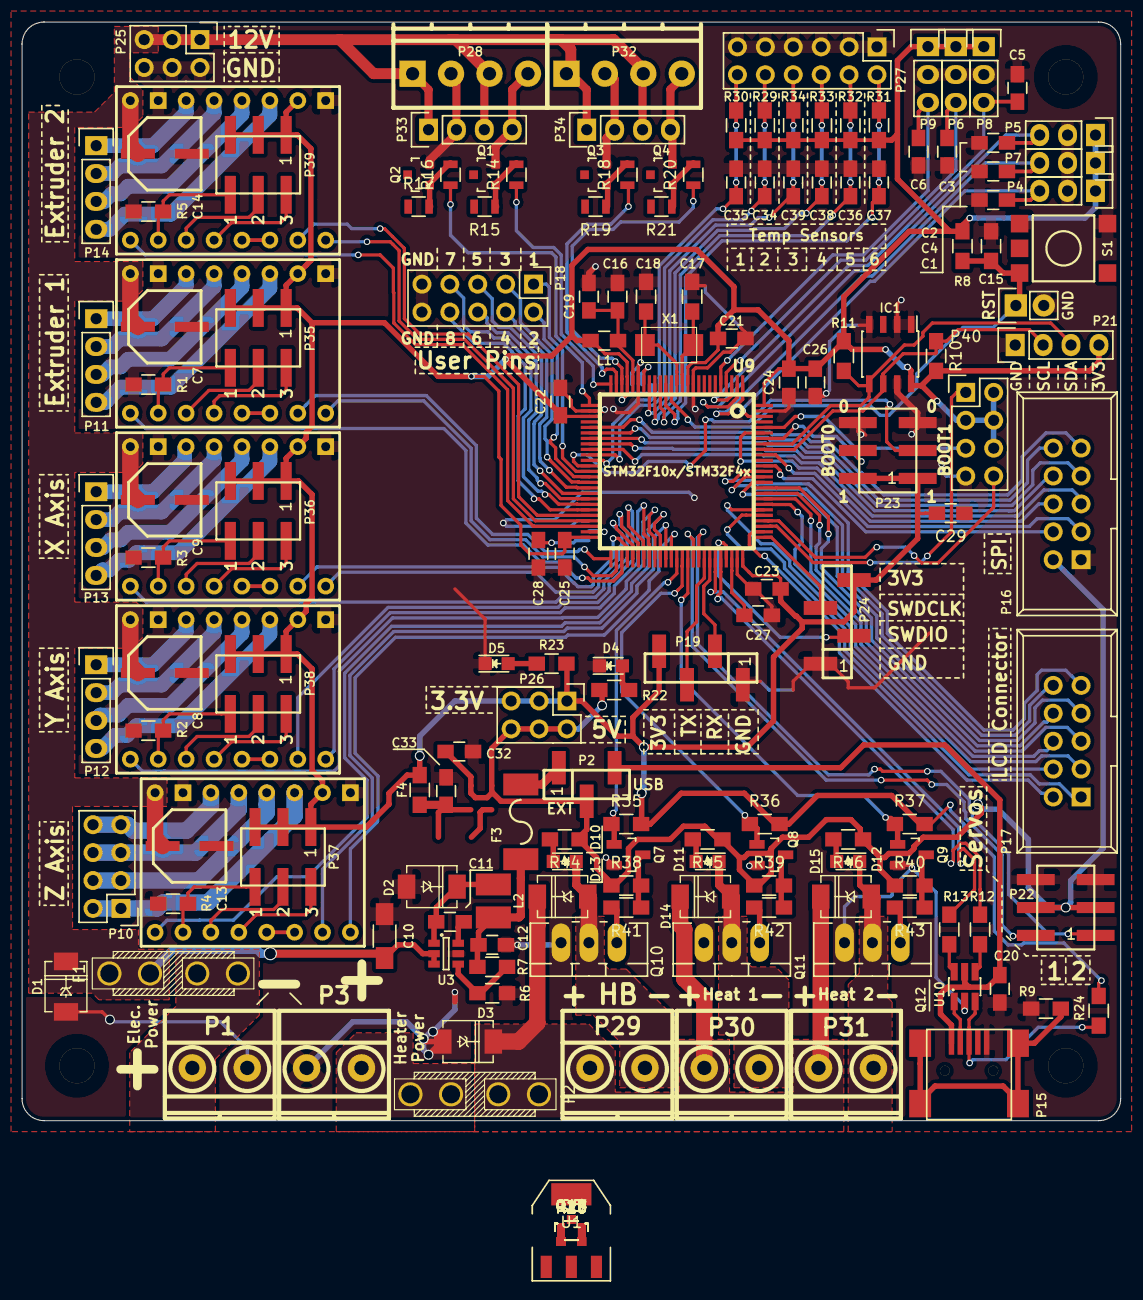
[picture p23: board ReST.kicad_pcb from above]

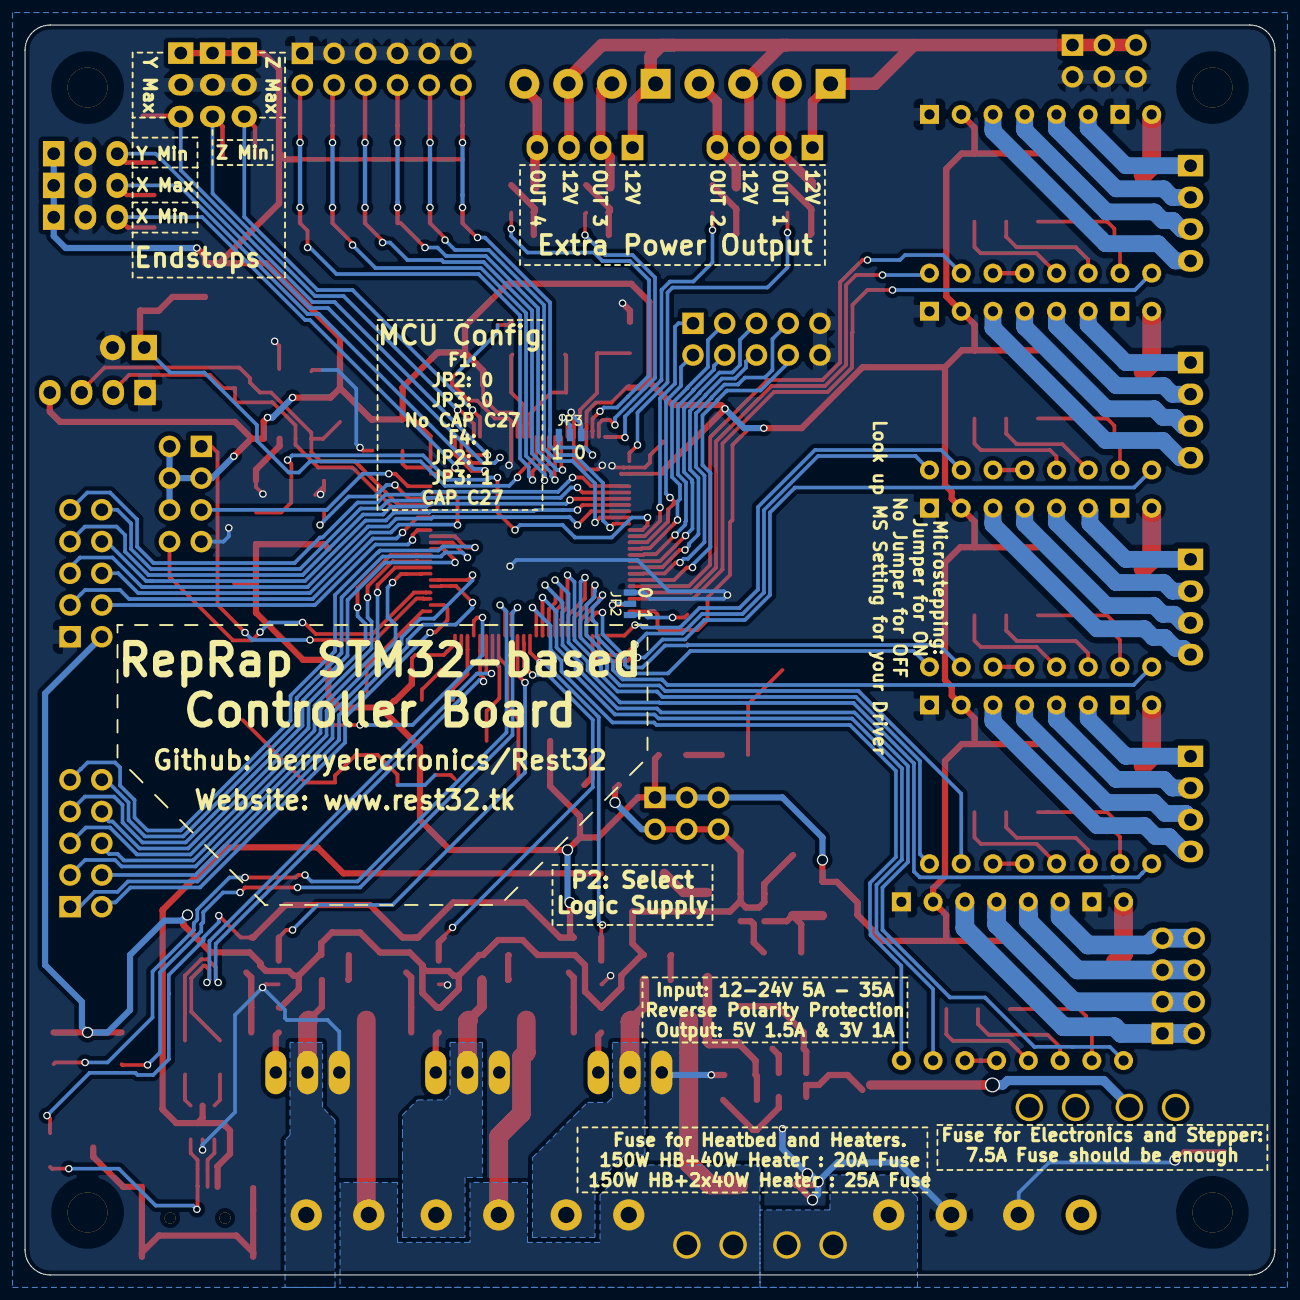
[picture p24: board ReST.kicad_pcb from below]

Board: 2 copper layers, 100.0 x 100.0 mm, 168 parts (2 on the bottom side), 168 nets.

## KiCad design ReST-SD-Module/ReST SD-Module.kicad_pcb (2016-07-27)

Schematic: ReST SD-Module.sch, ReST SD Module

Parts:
C1: 2.2uF; TantalC_SizeA_EIA-3216_HandSoldering
CON1, CON2: uSD_Card; SD_Card_Receptacle
D1: Led_Small; LED_0805
P1: CONN_02X05; Pin_Header_Straight_2x05
R2: 1K; R_0805_HandSoldering
U1: MIC5205; SOT-23-5

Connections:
+3V3: C1.1, CON1.4 (VDD), CON2.4 (VDD), R2.1, U1.5
+5V: P1.2, U1.1, U1.3
/SPI-CS: CON1.2 (CD/DAT3), CON2.2 (CD/DAT3), P1.8
/SPI-MISO: CON1.7 (DAT0), CON2.7 (DAT0), P1.10
/SPI-MOSI: CON1.3 (CMD), CON2.3 (CMD), P1.7
/SPI-SCK: CON1.5 (CLK), CON2.5 (CLK), P1.9
GND: C1.2, CON1.6 (VSS), CON1.10 (SHELL1), CON1.11 (SHELL2), CON1.12 (SHELL3), CON1.13 (SHELL4), CON2.6 (VSS), CON2.10 (SHELL1), CON2.11 (SHELL2), CON2.12 (SHELL3), CON2.13 (SHELL4), D1.1 (K), P1.1, U1.2
unnamed: D1.2 (A), R2.2

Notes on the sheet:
ReST Connector
Power Flag
SD Card
Power LED
Power Suppy

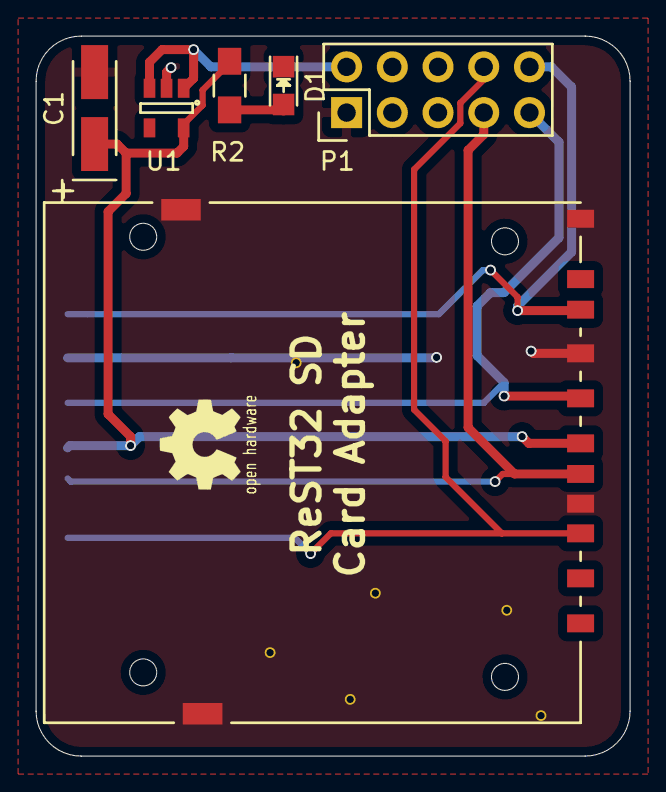
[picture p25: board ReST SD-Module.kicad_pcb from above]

Board: 2 copper layers, 33.0 x 40.0 mm, 7 parts (1 on the bottom side), 8 nets.

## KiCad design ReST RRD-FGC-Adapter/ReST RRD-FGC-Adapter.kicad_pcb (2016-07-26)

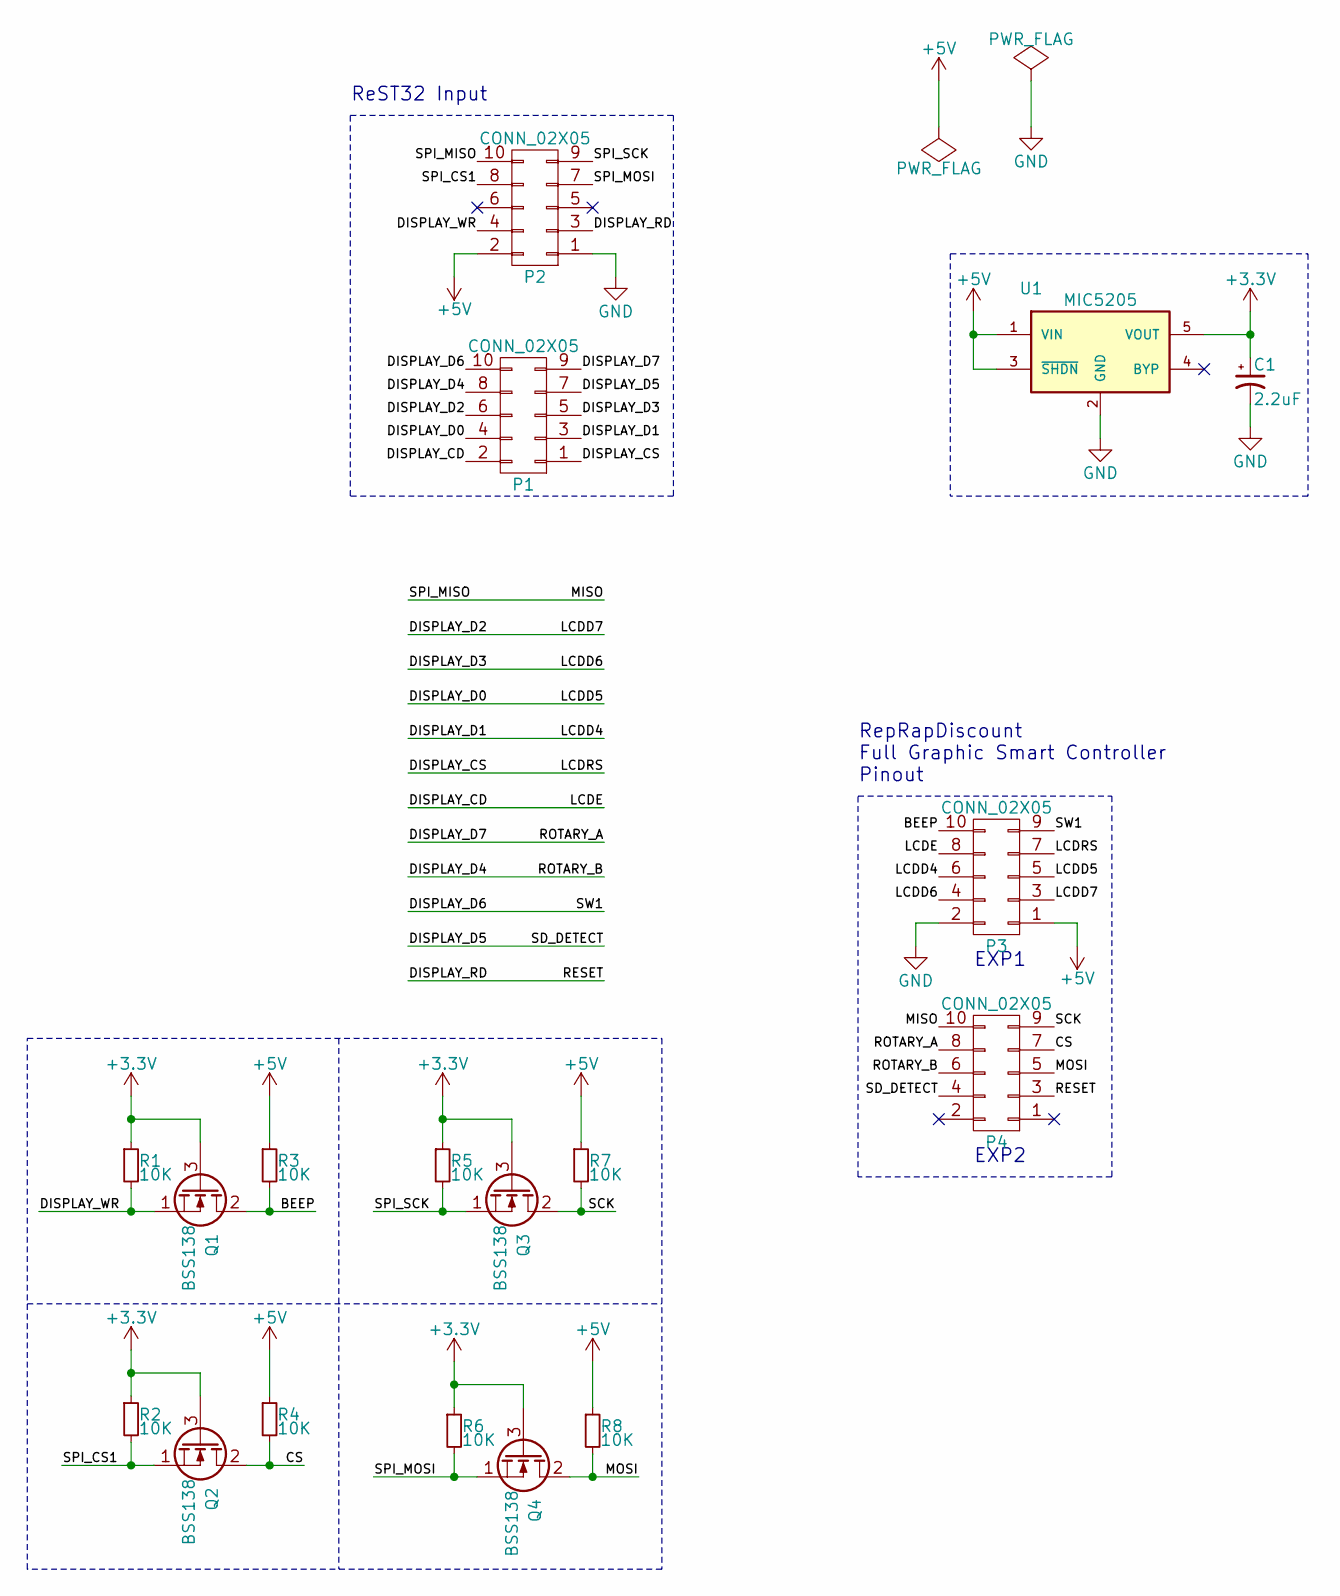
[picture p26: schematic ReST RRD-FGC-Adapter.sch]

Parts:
C1: 2.2uF; TantalC_SizeA_EIA-3216_HandSoldering
P1, P2: CONN_02X05; Pin_Header_Straight_2x05
P3, P4: CONN_02X05; IDC_Header_Straight_10pins
Q1, Q2, Q3, Q4: BSS138; SOT-23_Handsoldering
R1, R2, R3, R4, R5, R6, R7, R8: 10K; R_0805_HandSoldering
U1: MIC5205; SOT-23-5

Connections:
+3V3: C1.1, Q1.3 (G), Q2.3 (G), Q3.3 (G), Q4.3 (G), R1.1, R2.1, R5.1, R6.1, U1.5 (VOUT)
+5V: P2.2, P3.1, R3.1, R4.1, R7.1, R8.1, U1.1 (VIN), U1.3 (~SHDN~)
/BEEP: P3.10, Q1.2 (D), R3.2
/CS: P4.7, Q2.2 (D), R4.2
/DISPLAY_CD: P1.2, P3.8
/DISPLAY_CS: P1.1, P3.7
/DISPLAY_D0: P1.4, P3.5
/DISPLAY_D1: P1.3, P3.6
/DISPLAY_D2: P1.6, P3.3
/DISPLAY_D3: P1.5, P3.4
/DISPLAY_D4: P1.8, P4.6
/DISPLAY_D5: P1.7, P4.4
/DISPLAY_D6: P1.10, P3.9
/DISPLAY_D7: P1.9, P4.8
/DISPLAY_RD: P2.3, P4.3
/DISPLAY_WR: P2.4, Q1.1 (S), R1.2
/MISO: P2.10, P4.10
/MOSI: P4.5, Q4.2 (D), R8.2
/SCK: P4.9, Q3.2 (D), R7.2
/SPI_CS1: P2.8, Q2.1 (S), R2.2
/SPI_MOSI: P2.7, Q4.1 (S), R6.2
/SPI_SCK: P2.9, Q3.1 (S), R5.2
GND: C1.2, P2.1, P3.2, U1.2 (GND)

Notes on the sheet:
ReST32 Input
EXP1
EXP2
RepRapDiscount Full Graphic Smart Controller Pinout

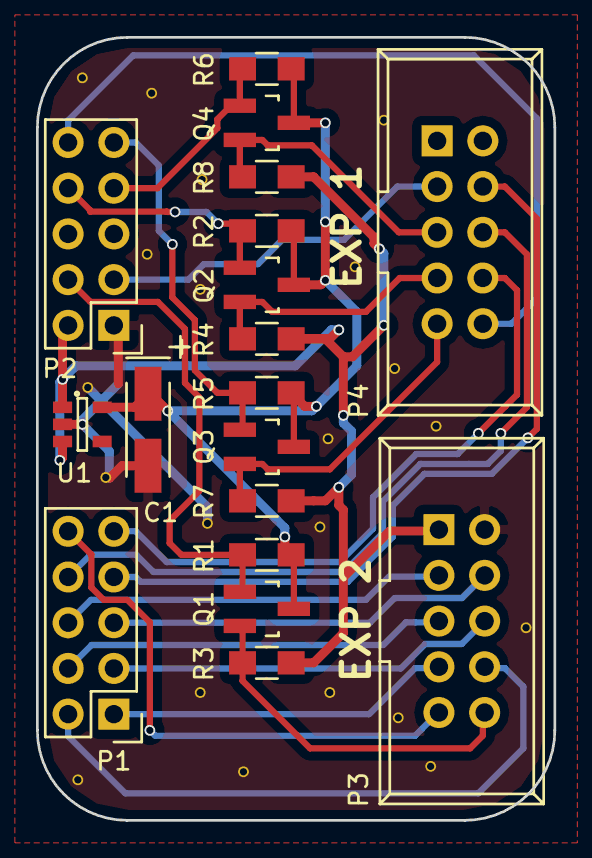
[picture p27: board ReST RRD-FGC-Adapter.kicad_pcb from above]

Board: 2 copper layers, 28.8 x 43.5 mm, 18 parts (0 on the bottom side), 23 nets.

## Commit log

2016-01-26 Initial Commit
    Added Schematics for Heatbed Module and Mainboard
    [ReST.kicad_pcb, ReST.sch, Rest-Heatbed-Module.kicad_pcb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]
2016-01-27 Changes Heatbed + Added Driver Board
    Edited Heatbed SMD Footprint from 0805 to 1206, easier to solder for beginners.
    Added Schematic and Netlist for Pololu Driver Board
    [Pololu.kicad_pcb, Pololu.sch, ReST.kicad_pcb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]
2016-01-29 Layout for Heatbed PCB
    Basic layout for the heatbed pcb is finished. single sided load, so its easier for reflow. need to work on the traces now. size shouldnt change by now.
    [Rest-Heatbed-Module.kicad_pcb, Rest-Heatbed-Module.sch]
2016-01-29 Moved Folders + Heatbed PCB Finished
    If there is any problem, please post an issue or write a post on the stm32duino forum. I can assure there is going to be a problem again with the libraries used, would really appreciate it to get some suggestions onto how to manage that
    [Pololu.kicad_pcb, Pololu.sch, ReST.kicad_pcb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]
2016-01-30 Added Heater Module Schematic + PCB
    Basically its the Heatbed Module but without the fuse (which is going onto the main controller) and without the external VIN, gets power from Pinheader.
    Should be capable of up to 5A if the female pinheader can handle 1A per pin, which seems to be common, but you never know..
    [Rest-Heater-Module.kicad_pcb, Rest-Heater-Module.sch]
2016-01-30 Added Pololu Driver PCB
    Size is 3.5cm * 3.75cm
    Im pretty happy with that size
    [Pololu.kicad_pcb, Pololu.sch]
2016-01-30 Changed minor issues in the Pololu Driver.
    Heatbed wont get much smaller. Finished Dimensions:
    Heatbed: 30,4mm * 47,8mm
    Heater: 29mm * 34,1mm
    Pololu: 36,3mm * 35,2mm
    [Pololu.kicad_pcb, Pololu.sch, Rest-Heatbed-Module.kicad_pcb]
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2016-02-02 Fixed GND Connection on ADD Board
    [ReST-Additional-Module.kicad_pcb]
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2016-02-06 Changes to the mainboard
    removed the pololu connector, added it onboard. added 5V regulator. need to add 3.3V Regulator and more pinout (Bluetooth, SWD, Boot0/Boot1 and more)
    [ReST.sch]
2016-02-08 Added Buck & Power Pins
    Buck Converter Added (Still need work on Diode, have to do the math later)
    Power Distribution Pins added (4 Pins of GND 12V 5V 3V3 each) for convenience (Leds and whatnot)
    [ReST.sch]
2016-02-08 Added A possible Pinout Table + Removed Pololu Driver Board
    [Pololu.kicad_pcb, Pololu.sch, ReST32 Pinout.xlsx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]
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2016-02-15 Changed Additional-Board and Pinout
    Sooo... I thought adding multiple Additional Module Boards would be bit much. Looked back at some older projects of mine and thought that using something like the uln2803 would be pretty neat (like 8 NPN Transitors, each 500mah and that in a DIL-18 Package IIRC) Which turns price really down, aswell as the size of the module.
    But using that one resultet in removing many extra pinouts, leaving with only 5 unused pins which will be broken out extra. This may change when the lcd pinout is finished. adding extra pinout for the additional board could also work out (as it occupies 8 pwm pins). I will look to copy that all into the schematic
    Also missing: I2C E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
    [ReST-Additional-Module.kicad_pcb, ReST-Additional-Module.sch, ReST.sch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]
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2016-02-15 Added Pin Def. on Mainboard + EEPROM
    FInishing of for today:
    copied the pin def. of the mainboard and added a eeprom (AT24C128)
    [ReST.sch, _saved_ReST.sch]
2016-02-21 Changed ADD Board to use less Pins
    Now only 4 Channels, but everyone ~0.6A capable
    [ReST-Additional-Module.kicad_pcb, ReST-Additional-Module.sch]
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2016-02-22 Loaded Netlist into PCB and laid it all out
    [ReST.kicad_pcb]
2016-02-27 PRE-RELEASE Rev. A!
    Yay. I managed to finish the Main PCB over the night, must say, Im happy with it. Things that changed since the last release:
    Heater:
    -Heater Module uses less Pins
    - Much smaller Design now
    Heatbed & Additional Module:
    -Changed distance from Edge to first Pin from 2.5mm to 2mm (will be changed on other boards too)
    Mainboard:
    -Added I2C Pullups 4K7
    -Swapped Pins from Stepper, Heaters and Endstops around for easier PCB Design.
    -Finished Design (10cm x 10cm!)
    Added some 3D Models for testing. If someone has problems with loading some modules, please contact me! (or make a pull request with a better solution)
    [BOM.xlsx, ReST-Additional-Module.kicad_pcb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]
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2016-02-27 Added PDF for Pinout
    +removed images from logo
    [ReST.sch, ReST32 Pinout.xlsx]
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2016-02-28 Added BOM and changed Oscillator to Crystal
    [BOM.xlsx, ReST.kicad_pcb, ReST.sch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]
2016-02-28 Added Missing Screw Holes on main
    [ReST.kicad_pcb]
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2016-03-01 Removed unnecessary Libs and finished SD Card Module
    [ReST SD-Module.kicad_pcb, ReST SD-Module.sch, ReST-Additional-Module.sch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]
2016-03-05 Finally removed all unnecessary Libs and added Heatsink for 5V Regulator
    [ReST SD-Module.kicad_pcb, ReST-Additional-Module.kicad_pcb, ReST.kicad_pcb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]
2016-03-05 Added IRLML2502 Module and added Ground vias everywhere
    [ReST SD-Module.kicad_pcb, ReST-Additional-IRLML2502.kicad_pcb, ReST-Additional-IRLML2502.sch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]
2016-03-06 Added BOM for all Items + suggested Links
    [BOM.xlsx, ReST SD-Module.sch, ReST-Additional-IRLML2502.kicad_pcb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]
2016-03-06 Added relative paths and linked footprint to a extra repo
    hope i finally fixed the problem with missing libs. will try to add the
    3d views, too
    [ReST-Additional-IRLML2502.kicad_pcb, ReST.kicad_pcb, ReST.sch]
2016-03-07 Finished PCB design, notations and silkscreen
    gonna work to finish a combined design for cheaper pcb cost and put
    everything i need into the bom
    [ReST SD-Module.kicad_pcb, ReST-Additional-IRLML2502.kicad_pcb, ReST.kicad_pcb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]
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2016-03-09 Finished Combined PCB and Gerber files
    Combined pcb fits on 10x10cm, breakable and gerbers are finished for elecrow order. will order everything this weekend, lets see if it works.
    [BOM.xlsx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]
2016-05-13 Reworked Modules to sit ontop of the mainboard
    [BOM.xlsx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]
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2016-05-16 Rework. missing screws but everything else fits
    [ReST.kicad_pcb, ReST.sch]
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2016-05-30 Changes in Heatbed and Heater + F1 and F4 Pinout table with functions
    [F10x vs F4x.ods, ReST.sch, Rest-Heatbed-Module.kicad_pcb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]
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2016-07-10 Mostly finished with main PCB. Only need to work the High Current Stuff out. On Vacation for now
    [ReST.kicad_pcb, breakout.sch, extra_output.sch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]
2016-07-26 electrically finished. in the works of the silkscreening.
    Schematic for SD Card Adapter and a RepRapDiscount-Adapter in the works. but not in this commit
    [ReST-B.Cu.gbl, ReST-B.Mask.gbs, ReST-B.SilkS.gbo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]
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2016-07-26 removed copper and solder mask around screw holes
    [ReST-B.Cu.gbl, ReST-B.Mask.gbs, ReST-B.SilkS.gbo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]
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2016-07-26 Final Release
    With Mainboard, SD Card Adapter and Adapter for a RepRapDiscount Full Graphic Smart Controller
    The SD Card Socket can be soldered on the front or on the back, so that the user can insert the card either from top or from the botton, depending on how the controller is mounted.
    [BOM.xlsx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]
2016-07-26 forgot naming of the connector in the lcd adapter
    [ReST RRD-FGC-Adapter-B.Cu.gbl, ReST RRD-FGC-Adapter-B.Mask.gbs, ReST RRD-FGC-Adapter-B.SilkS.gbo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]
2016-07-26 added ESP-01 Support
    Afterthought, completely forgot about it
    [breakout.sch, extra_output.sch, heater.sch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]
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2016-07-27 added missing usb pullup
    [ReST RRD-FGC-Adapter.csv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]
2016-07-27 minor changes to values of components and footprints. added two leds for both 12V Rails.
    [ReST RRD-FGC-Adapter.csv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]
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2016-09-22 changes in footprints of heater part and misc. stuff
    [heater.sch]
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2016-09-23 changed extra output schematic
    added 3->5V level transtor. changed footprints. changed resistor
    footprints.
    [extra_output.sch]
2016-09-24 changed extra output circuit, removed 3.3V Buck and replaced with LDO
    [power_supply.sch]
2016-09-24 changed 3.3V LDO due to symbol errors
    [breakout.sch, extra_output.sch, logic.sch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]
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
